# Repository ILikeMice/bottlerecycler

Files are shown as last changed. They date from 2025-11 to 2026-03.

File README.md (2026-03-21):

# PETG to Filament Bottle recycler!

https://cad.onshape.com/documents/4bfb7a9ed6c6a0026068647e/w/94f532863257475cc59f14dc/e/ca07e4d33eb1537d07c3052b

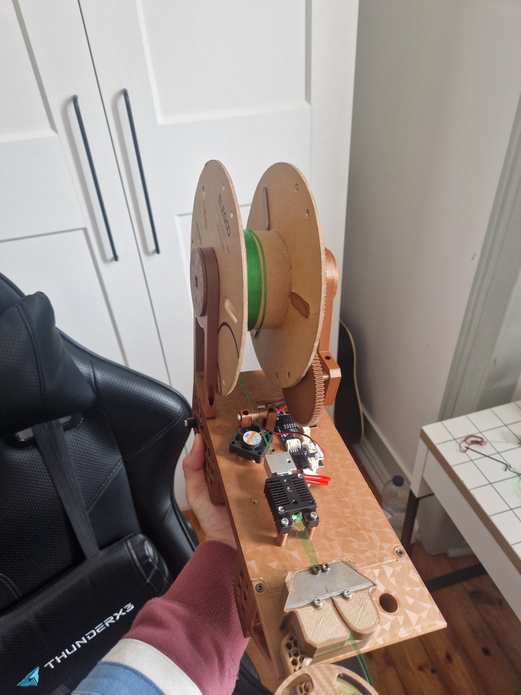
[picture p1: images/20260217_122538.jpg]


Name pretty much says it all, this is a project to try and recycle the mountain of iced tea bottles ive got into filament! Ive seen people do this years ago, but didnt really have any CAD or electronics skills back then, and really wanted to make something like that too, since 30€ per kg of filament seems overpriced and i would really prefer to spend my money on aliexpress instead.

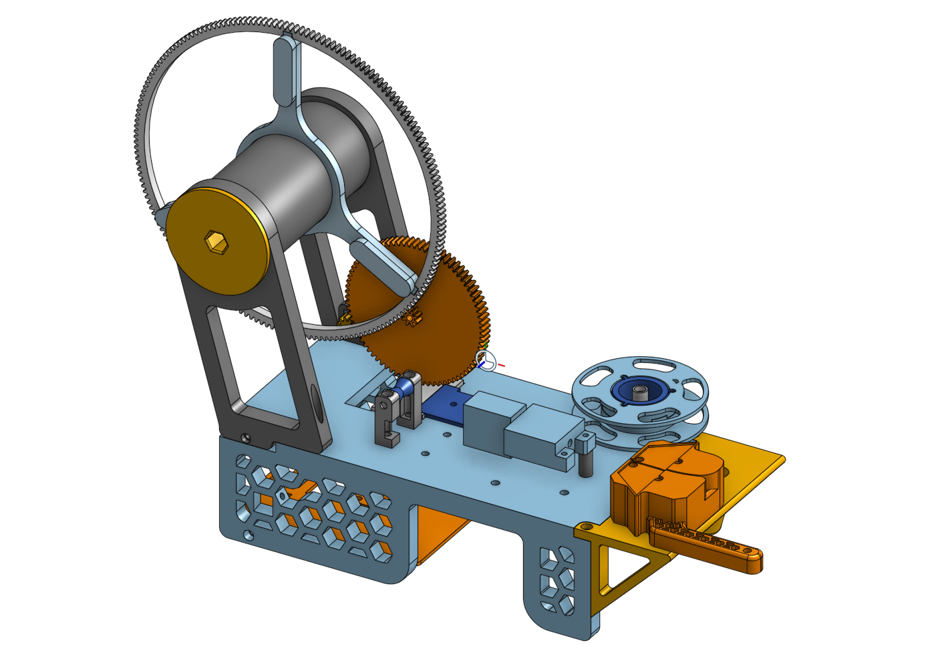
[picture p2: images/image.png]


The way it works is: plastic bottles get cut up into strips (~8mm) and pulled through the hotend, at a temp that is about enough to soften the plastic **without melting it**, so the strip gets rolled up into itself and forms some sort of a tube. I can then use this makeshift filament to print stuff!

I tried to use as many components from an Anycubic Kobra 2 Hotend in this project, since i had one laying around (and which i bought for only 10 bucks, damn good deal), and ended up using pretty much everything i could: The stepper motor from the extruder, the hotend itself(duh), practically all the screws, and even the PCB that controlled (or rather had all the connectors, the only thing except traces on that thing is a couple of diodes lol) the whole thing!

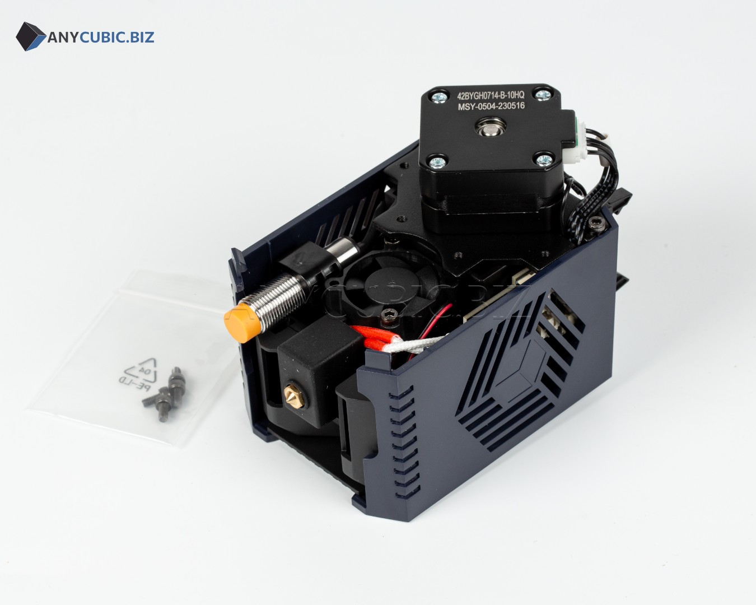
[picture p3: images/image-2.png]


The contraption itself is controlled by an ESP32, which drives a BJT for the DC motor of the spool and a Heater Element via a mosfet, with the circuit shown below!!

### Main Circuit
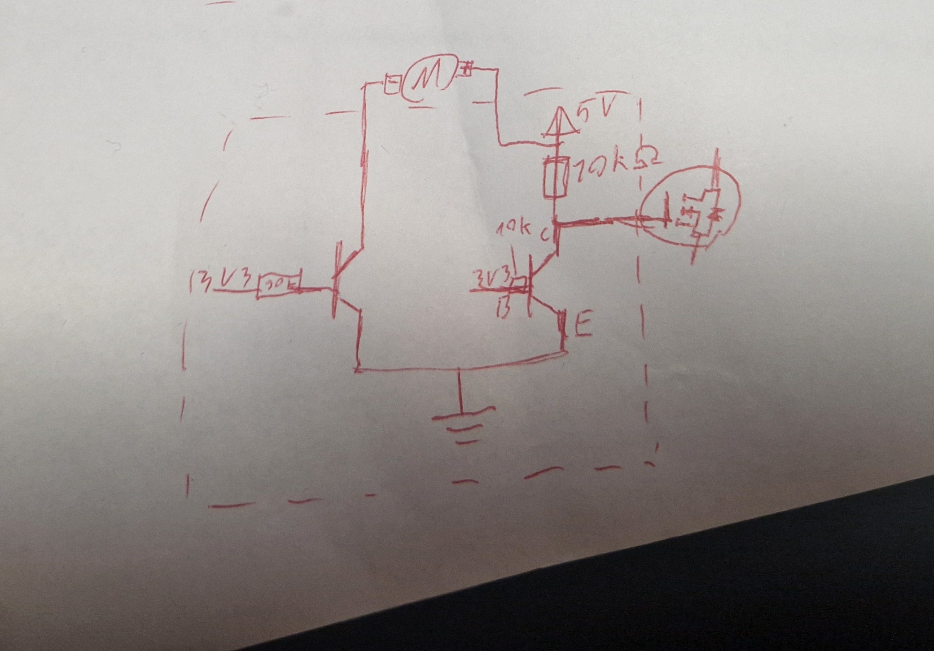
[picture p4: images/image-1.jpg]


This is the diagram of the main circuit im using, which i had to put together and solder on my own! You will also have to remove the ressistors on the IRF520 module. The circuit is used to drive the DC motor with 5v from the buck converter, and drive the MOSFET with the same 5v, since the ESP can only output up to 3.3v, and the IRF520 needs 4v  at gate.

## BOM

This is all the extra stuff i had to buy and didnt have around!

|Name |Cost (per unit. in €)|Amount|Cost (€)|Link |
|---|---|---|---|---|
|6A 24V PSU (laptop charger or sth)|15 |1 |15 |bought from local ebay |
|24V to 5A DC-DC converter |2.88 |1 |2.88 |https://www.aliexpress.com/item/1005007259901753.html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 |
|MOSFET Breakout |1.22 |1 |1.22 |https://www.aliexpress.com/item/1005008554454996.html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 |
|Trapezoidal Blade |0.89 |1 |0.89 |https://www.aliexpress.com/item/1005007677799664.html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 |
|Wire Crimps Set |3.69 |1 |3.69 |https://a.aliexpress.com/_EzglbQU |
|Stepped drill bit |1.09 |1 |1.09 |https://a.aliexpress.com/_EJElGGy |
|M3 nuts |0.39 |1 |0.39 |https://a.aliexpress.com/_EuZlNXO |
|Kobra 2 hotend. bought from ebay  |10 |1 |10 | |
|L298N |2.67 |1 |2.67 |https://pt.aliexpress.com/item/1005009503497796.html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 |
|ESP32 |3 |1 |3 |https://pt.aliexpress.com/item/1005008889768599.html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|
| | | | | |
| |Total (€): |39.81 | | |

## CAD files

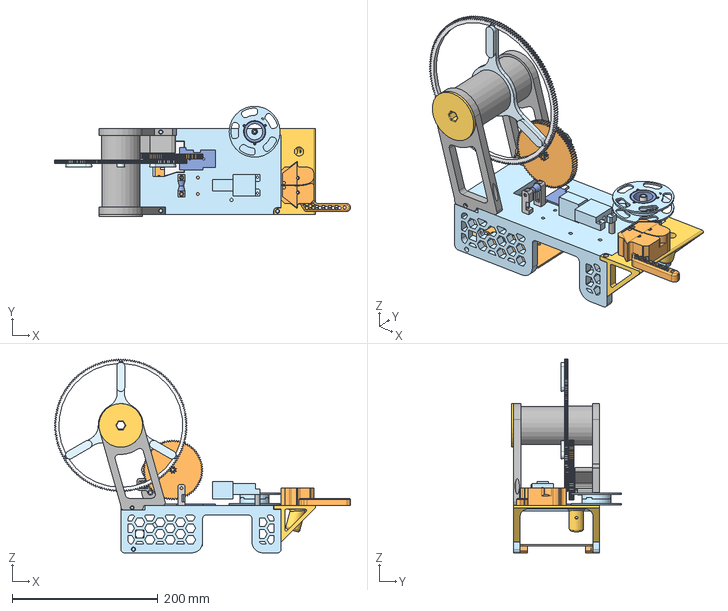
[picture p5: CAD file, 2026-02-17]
CAD/BottleToPETG(1).step
406.3 x 151.2 x 266.0 mm

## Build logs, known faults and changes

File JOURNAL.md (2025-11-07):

<!--
  ===================    !!READ THIS NOTICE!!   ====================
  DO NOT edit this file manually. Your changes WILL BE OVERWRITTEN!
  This journal is auto generated and updated by Hack Club Blueprint.
  To edit this file, please edit your journal entries on Blueprint.
  ==================================================================
-->

## 11/1/2025 3 PM - Initial research!  

Ive got an overall idea on how a pet bottle recycler works, but never really looked into the details much. I think before starting the modelling, etc. itd be better to get some info for potential future struggles and so on.
All i know so far about the process is: bottle gets sliced into strips, pulled thru an extruder and then wound onto a spool. 
After watching a bunch of vids on ppl assembling pet recyclers (didnt really get as many about the design process itself, but thats my task after all, also [this one](https://www.youtube.com/watch?v=1yIe1Pp_Nrg) was the coolest one i found, will probably be using it as a reference mainly, even though it might not be fully printed like i want it), i got an approximate plan? I can slice the bottle with some sanded bearings (which i think is really cool, i only thought of using a blade b4), as for the heating part, im currently trying to deconstruct the kobra hotend. Also, i think ill try to make this thing as compact as possible, since i dont have much space in my room :pf:

Probably the inspo ill be using throughout the project: 


## 11/1/2025 9 PM - Hotend!  




Managed to fully take apart the hotend, surprisingly without breaking anything (and did some browsing on aliexpress for the parts i dont yet have) ! Its got a pcb with some ressistors, but those seem to be for the levelling sensor, so im unsure whether ill use it or just detach all the things from it. 
After some more digging, i found out that the hotend runs at 24V, so ill need a 24V psu, but im willing to pay for all that stuff. The benefit of using the pcb though would be having every connection neatly mounted already, so on second thoughr ill try and stick with that, not like its got any other use. 
Also, while taking the thing apart, i noticed that the steppers casing is grounded for some reason (weird to me, but ill probs keep that just to be safe :p ) also would probably need to make some drilling changes for the hotend, either drill a slightly bigger intake hole with a stepless bit, or if i dont feel like drilling i might try making that transition with a 3d printed part (my own idea wow), and ill defo need to make a 1.7mm hole in the nozzle ive got already. 

Speaking again of the pcb, its got a weird mount for all the cables, but a simple jumper cable seems to fit it, but ill have to design some frame to hold them all so i can clamp them with the things at the mount. Would be cool to use though.  

## 11/2/2025 12 AM - more research yippie  

I know i need a 24V PSU, but i have no idea so far how strong it should be. since i want this to be as compact as possible, im hoping for 3A at best, 5A max. Above that the psu gets a bit big (3A is 110\*78\*36, 5A is 160\*98\*42mm, 6A is 199\*98\*42mm). After a quite some research i found that the hotend altogether is supposed to be about 24/60W, which is about 2.5A already. Also checked on the heating element itself (which gave me 60w) to confirm the power and the fact its the hotend only, not the whole toolhead with stepper and so on. I couldnt find anything googling the numbers on the stepper to get its approximate power, so i had to turn to deepseek my beloved. It suggested a max current of .66A per phase, so 1.32A max in total, so ill stick to that for now (writing on the nema17 was **_42shdb0066z-10WD_**). After detaching the small fan attached to the heatsink, i could read off 0.08A/24V from it. I could also use the bigger fan there, but itll need .2A of current, so i gotta see if ive got enough left at the end. So for now, the total current is at about **3.9A** (with the smaller fan, with the bigger one its **4.02A**). Id like some wiggle room for the controlling stuff (which i gotta power with a stepdown converter), so i think 5A should hopefully be enough. I dont need anything fancy to control the stepper, ill use a L298N driver that ive got laying around. Speaking of logic and control though, ill need something to actually control all the stuff. I could go with an orph pico ive got but that would mean id need a display, and i sadly dont have one right now (altho it would be cool to use one bc yk, this is a hc ysws). An alternative would be an ESP32/rpi zero 2 W that i gotta control via ssh or so, which would save me like 3 bucks in buttons and display. tempting. Although a display would look cooler.




## 11/2/2025 3 PM - CAD start  

After trying around a bit in freecad and taking 8 fucking minutes to make a single rectangle, i decided that i dont like freecad anymore and am switching to onshape. I did some irl mockups of how the hotend and so on could be placed, and the two options i had was either with the fan facing downwards, but pcb being below the hotend, or fan upwards and pcb being higher than the hotend, since i cant really move it much due to the cables. I tried reattaching the fan on the other side of the heatsink so it could be on top with the pcb on the bottom, but had to kinda force the screw into it from the other side to make the thread useable, no idea why they made it like that. 
Anyways, after doing that, the layout of the components seems perfectly useable, i need the hotend to be higher than the pcb because i gotta get it as far away from the plasic parts as possible, while preferrably having the pcb inside the casing. I made an approximate model of the whole hotend part in onshape, with the main details ill need for mounting, etc. Took a bit longer than estimated, since i had to get used to onshape, but overall onshape seems pretty nice. 







## 11/2/2025 9 PM - More CAD!  



Thought of how id design the casing.[ In the video i mentioned in the first devlog](https://www.youtube.com/watch?v=1yIe1Pp_Nrg), the guy was using extrusions and kinda just mounting everything on that. As cool as i thought having extrusions would be, i wanna make this as 3d printable and cheap as possible. My current idea is to have little platforms or pins to hold the psu and so on, that ill screw into the sides of the rectangular ish casing (without a bottom, to reduce material), still thinking on that though. 

Either way, main thing this session was cadding the pcb so i can make a mount for it or so. That took me waaaayyy too long since there wasnt ANY info on it online, so i had to measure anything manually (and of course i fucked up a couple times, and had constraint errors everywhere T-T, also i realized ive never really modelled after a real life complex-ish object without a schematic). After fixing everything though, it looks pretty nice and im happy with it. I wanna also make mounts ish for every pcb ill have, since this thing might be moved around a bunch and i wouldnt want the stuff to slip.  

## 11/3/2025 - Casing stuff!  





^^As you can see above, i did a bunch of improvements on the casing! Taking inspo from the design of that other guy i mentioned in the first entry, i wanted some sort of hex pattern on the casing, which looks cool but is also mainly to save some filament and printing time. Ive never really printed anything vertically with a hex pattern, and was unsure if it would hold at all. Some research told me i gotta have the flat side of the hexagon pointing up, and just bridge over it so it doesnt break. I have no idea how my printer performs in bridging, but from what ive seen online the quality is pretty meh, but using supports might just increase print  time and filament use more than this pattern is reducing. The upper version is me trying to round the corners to minimize bridging, but that way just leads to circles at the end, and im unsure of what the layer height req will be with rounded corners (does also look pretty cool tho!). Gotta run some tests ig.



Also, i got started on the electronics layout stuff and so on! Added some cool looking holders! The orange ones will be secured in place with the 2 heatset inserts and some screws ive got in the hotend/some other way, but ill be sure to definetly use those inserts, thought its really neat to use as much from the toolhead as possible. The blue ones are printed together with the case (i thought of making them flipped, so i wouldnt need support but that seemed like a pretty bad idea holding power wise) and are gonna need supports, so i placed them on the edges to be able to not have supports placed on the model itself.

PS: this shit took me way too long, im not adding all the variations i tried here and holy some of the tools (esp pattern) are so much weirder than in fusion, this shit is making me actually learn how to use constrains in sketches lmao

## 11/4/2025 - Electronics layout stuff (yay..)  



I did some of the work here yesterday, but was too tired to document it :p

First of all, made holes for screws/heatset inserts to mount the pcb and hotend (also made a hole for the pcb wire holder thing so i can connect stuff from the electronics inside the case into it)! Had to correct some little errors in the pcb model since im that good at cad. Also, minor change, changed the shape of the electonics holder mount, since printing circles would be pretty annoying and probs unstable.



Really love how i can modify the timeline to change some stuff, didnt really do that much in fusion, does take some extra time sometimes tho, but feels waaay cleaner




So, electronics layout! Dont wanna flood the whole page with the shit i tried before giving up and looking for an algorithm to find the optimal layout for me (almost pulled up python smh), the first img is one of the first things i tried making and was confident enough in to screenshot! I was then hit by the psu that i hid which was taking up too much of the space. My fault for hoping i could fit all the stuff on 1 platform ig. I was still hanging onto the idea of fitting it all on the platform for a while, all i needed was like 3mm of extra space. I then proceeded to resize the whole case (which was really painful since i also had to change the pattern thing) only to realize that its 223mm long now. Which just so happens to be about 3mm bigger than my printbed. Yeouch. The whole thing is like 110mm wide so i dont think placing it diagonally would fit it onto the printbed either. Started thinking of where i could possibly place 1 more component, first idea was to make the platform have 2 floors, but that seemed rly hard to print and overall i am not dealing with the wires on 2 whole floors. Other option would be to mount it somewhere on the case (if so, then probably on the "ceiling" of the case, since anywhere else would be too far from the components (e.g. i need the 24 to 5v converter to be not far from the esp in order to power it, and other components like the mosfet or L298N near the PSU cuz i need 24v there). After more pondering and messing around for a fuckton of time, i went with the L298N on the ceiling, and the rest on the Platform (dont have mounting holes for the components figured out yet, will after most of them arrive)  

## 11/6/2025 - Filament spool mount!  

Yippie 2 in 1 journal entry again! 
Final design today below:



Yesterday, i made the side things that are supposed to hold the spool up, see how theres like half the thing popping out at the bottom? I probably couldve just not done that but i wanted to make sure this shit does NOT wiggle, and even tho inserting a bolt from that side makes the main case look weird in places, i think its probs def better with that side mount (i still gotta add a screw to hold it down like one normally would). 

Initially, the plan for the spool was for it to be halfway "inside" the case, kinda submerged for compactness. Only reason i cant do that though is thanks to the electronics layout problem (not reexplaining that, go read previous entries) taking up way too much space, and removing any more of the case would just screw up the stability of it.



^^weird case thing because of the sideways screw, hopefully it wont break (surely not foreshadowing, _**right**_?)^^

Then today, i also did some more research on how people overall made this part. Once again taking inspo from the main inspiration design, i saw hes got a 3d printed spool and a huuuge gear around it connected to a smaller stepper gear. As much as i want to make this fully 3d printable, i did have a spool with just a bit of filament left int it. After removing that, i saved myself like 6-7 hours of print time! The spool has round holes in it, 6 in total, paired together in 3 pairs. My initial idea was to make things that clamp into those, holding a gear that i can later rotate somehow. I ended up thinking about that in the very last step, will return to this in like 1 paragraph.

I was now also stuck with a decision: either i connect the spool with a timing belt (my initial idea) or i make a huge gear thats exactly the same module as the one mounted on the stepper (cant take off the gear sadly, its part of the stepper rod :p). The timing belt did fit onto the stepper gear decently though, and that extra closed loop belt i bought was reeeealllly looking at me. biggest gear i could do with that belt was about 80T though, and the stepper ended up being way too far from the pcb :/ I didnt really want to do a big gear, since first of all, id have to print a decently big chunk of it with the smallest nozzle ive got (0.2mm), and prototyping didnt sound much fun with that either. After trying around some more though, i realized i didnt really have a choice, so i just went with that, and make a whopping 400T gear (it had to be big enough to read anywhere near the PCB) that made onshape lag yayyy! Also, decided to mount the stepper directly to one of the spool holders, since i dont think i really need a stepper frame here. I did have to manually measure everything on the stepper tho since i dont trust online sources on some random stepper that i dont have a 20823 page manual for. In total, i am left with a 40:1 reduction ratio on that thing, surely thats fine.

Back to attaching the gear to the spool! I tried using those 6 holes, but they were so conveniently placed for my inconvenience, that the teeth were right in the middle of them. Instead of trying to get it to work i just switched to the 3 rectangular ish holes on the spool. My idea of having the mounts outside the gear didnt really work with that one, i think its even better this way though, lucky the 1st version didnt work! 

The blue thing is the thing that attaches to the filament spool. Ill print it with a bigger nozzle to save time and just glue it onto the gear thing.

Biggest problem so far though was the layout of the stuff on that cylinder thats holding everything. i wanted to make everything not slip, and make sure the rod itself is somewhat detachable too, since ill need to remove the spool for, you know, printing sometime. Long story short, in the end i ended up with a design looking like a spyglass, where the things have a decreasing diameter, so theyre practically locked in place/sqished into the one holder!



Also, the spool isnt perfectly centered now, so i had to move the hotend a bit.



## 11/7/2025 - Cutting mechanism test!  

I think the winding system is pretty much done, just gotta add in some screws and maybe polish it a bit. Anyways, i wanted to test whether bearings could even cut the bottle, so i took some sandpaper and started sanding one!

I realized quite quickly that theres a reason everyone in the videos had either a belt sander or some disk thing, since sanding this thing manually was real hard, and took me like one hour in total.

Screenshot_20251107_144942_YouTube


^^ bearing in the video vs my bearing after goinf through a whole sheet of sandpaper and exhausting my hand

Ended up almost losing the bearing towards the end under the boards of the balcony (went there to not disturb anyone, this process is pretty damn loud), luckily managed to retrieve it though

In conclusion: im gonna assume it works, since compared to the unsharpened side of the bearing, the sharpened one actually leaves some scratches on the bottle, so surely itll work if i sand it just a bit more, right?

Also, im gonna try making some holder i can attach to my drill to sand this thing, no way im doing all that manually again.

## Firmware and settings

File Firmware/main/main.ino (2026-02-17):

#include <ESP8266WiFi.h>
#include <ESP8266WebServer.h>
#include <math.h>

#define THERMISTOR_PIN A0
#define MOTOR_PWM_PIN 4      // D2 pin
#define HEATER_PIN 14        // D5 pni

const char* ssid = "ssid!";
const char* password = "your pwd";

ESP8266WebServer server(80);

// this changes probably if youre using a diff thermistor!!!!
#define SERIES_RESISTOR 100000.0
#define NOMINAL_RESISTANCE 100000.0
#define NOMINAL_TEMP 25.0
#define BETA_COEFFICIENT 3950.0

#define HEATER_WINDOW_MS 1000  
#define MAX_HEATER_DUTY 200   

float Kp = 2.0;
float Ki = 1.5;
float Kd = 0.1;

// this prolly also varies depending on your hardware, but i dont think theres any case in which youll need 260C for this.
#define MAX_TEMP 260.0
#define PID_MIN_OUTPUT 0
#define PID_MAX_OUTPUT 255

float currentTempC = 0.0;
float targetTempC = 200.0;
bool autoMode = true;       
bool heaterEnabled = false;  
bool emergencyStop = false;
bool motorRunning = false;

float pidInput, pidOutput, pidSetpoint;
float lastError = 0;
float integral = 0;
unsigned long lastPidTime = 0;

float heaterDutyCycle = 0;  
unsigned long heaterWindowStart = 0;

float tempAtHeatStart = 0;
unsigned long heatStartTime = 0;
bool isHeating = false;

unsigned long lastDebug = 0;

void readTemperature() {
  const int SAMPLES = 20;
  long sum = 0;
  
  for (int i = 0; i < SAMPLES; i++) {
    sum += analogRead(THERMISTOR_PIN);
    delay(2);
  }
  
  float currentADC = sum / SAMPLES;
  
  float reading = (1023.0 / currentADC) - 1.0;
  reading = SERIES_RESISTOR / reading;
  float thermistorResistance = reading;
  float steinhart = thermistorResistance / NOMINAL_RESISTANCE;
  steinhart = log(steinhart);
  steinhart /= BETA_COEFFICIENT;
  steinhart += 1.0 / (NOMINAL_TEMP + 273.15);
  steinhart = 1.0 / steinhart;
  currentTempC = steinhart - 273.15;
  
  if (millis() - lastDebug >= 2000) {
    Serial.print("ADC:");
    Serial.print((int)currentADC);
    Serial.print(" R:");
    Serial.print((int)thermistorResistance);
    Serial.print(" temp:");
    Serial.print(currentTempC, 1);
    Serial.print("target:");
    Serial.print(targetTempC, 0);
    Serial.print("heater duty:");
    Serial.print((int)heaterDutyCycle);
    Serial.print("/255");
    if (autoMode) Serial.print(" AUTO");
    else Serial.print(" MANUAL");
    if (emergencyStop) Serial.print(" EMERGENCY");
    Serial.println();
    lastDebug = millis();
  }
}

void updatePID() {
  unsigned long now = millis();
  if (now - lastPidTime < 200) return;
  lastPidTime = now;
  
  if (!autoMode || emergencyStop || !heaterEnabled) {
    if (!heaterEnabled && autoMode) {
      heaterDutyCycle = 0;
    }
    return;
  }
  
  pidInput = currentTempC;
  pidSetpoint = targetTempC;
  
  float error = pidSetpoint - pidInput;
  
  if (abs(error) < 50) {
    integral += error * 0.2;  
  }
  integral = constrain(integral, 0, 100);
  
  float derivative = (error - lastError) / 0.2; 
  lastError = error;
  float output = (Kp * error) + (Ki * integral) + (Kd * derivative);
  output = constrain(output, PID_MIN_OUTPUT, MAX_HEATER_DUTY);
  heaterDutyCycle = output;
  
  if (heaterDutyCycle > 50) {
    if (!isHeating) {
      isHeating = true;
      tempAtHeatStart = currentTempC;
      heatStartTime = millis();
    }
  } else {
    isHeating = false;
  }
}

void updateHeater() {
  unsigned long now = millis();
  
  if (now - heaterWindowStart > HEATER_WINDOW_MS) {
    heaterWindowStart = now;
  }
  
  int onTime = (heaterDutyCycle / 255.0) * HEATER_WINDOW_MS;
  
  if (!emergencyStop && (heaterEnabled || (autoMode && heaterDutyCycle > 0))) {
    if (now - heaterWindowStart < onTime) {
      digitalWrite(HEATER_PIN, LOW);
    } else {
      digitalWrite(HEATER_PIN, HIGH); 
    }
  } else {
    digitalWrite(HEATER_PIN, HIGH);    
  }
}

void checkSafety() {
  if (currentTempC > MAX_TEMP) {
    emergencyStop = true;
    heaterEnabled = false;
    heaterDutyCycle = 0;
    digitalWrite(HEATER_PIN, HIGH);
  }
  
  if (isnan(currentTempC) || currentTempC < -10 || currentTempC > 350) {
    emergencyStop = true;
    heaterEnabled = false;
    heaterDutyCycle = 0;
    digitalWrite(HEATER_PIN, HIGH);
  }
  
}

void setMotor(bool state) {
  motorRunning = state;
  digitalWrite(MOTOR_PWM_PIN, state ? HIGH : LOW);
}

void setHeaterManual(bool state) {
  if (emergencyStop) return;
  autoMode = false;
  heaterEnabled = state;
  heaterDutyCycle = state ? MAX_HEATER_DUTY : 0;
}

void setHeaterAuto(bool enable) {
  if (emergencyStop) return;
  autoMode = true;
  heaterEnabled = enable;
  if (!enable) {
    heaterDutyCycle = 0;
    integral = 0;
    lastError = 0;
  }
}

void setTargetTemp(float temp) {
  targetTempC = constrain(temp, 0, 250);
  integral = 0;  
  lastError = 0;
}

void handleRoot() {
  String html = R"rawliteral(
<!DOCTYPE html>
<html>
<head>
  <meta name="viewport" content="width=device-width, initial-scale=1">
  <title>Extruder Control</title>
  <style>
    body { font-family: Arial; background: #1a1a1a; color: #fff; text-align: center; padding: 20px; }
    .emergency { background: #d32f2f; padding: 20px; font-size: 24px; cursor: pointer; 
                 margin-bottom: 20px; border-radius: 8px; font-weight: bold; }
    .grid { display: grid; grid-template-columns: 1fr 1fr; gap: 20px; max-width: 700px; margin: 0 auto; }
    .card { background: #333; padding: 20px; border-radius: 12px; }
    .temp { font-size: 48px; color: #ff9800; }
    .target { font-size: 36px; color: #4CAF50; }
    .status { font-size: 20px; margin: 10px 0; }
    .on { color: #4CAF50; }
    .off { color: #666; }
    .heating { color: #ff9800; }
    button { padding: 15px 30px; font-size: 16px; margin: 5px; border: none; 
             border-radius: 8px; cursor: pointer; }
    .heat-auto { background: #ff9800; color: #000; }
    .heat-man { background: #9c27b0; color: #fff; }
    .heat-off { background: #555; color: #fff; }
    .motor-on { background: #2196F3; color: #fff; }
    .motor-off { background: #555; color: #fff; }
    .pid-box { background: #222; padding: 10px; border-radius: 8px; margin-top: 10px; font-size: 14px; }
    input[type=number] { width: 60px; font-size: 16px; }
    .warning { color: #ff6b6b; font-weight: bold; margin-top: 10px; }
    .mode-auto { border: 2px solid #ff9800; }
    .mode-man { border: 2px solid #9c27b0; }
  </style>
</head>
<body>
  <h1>Extruder Control</h1>
  
  <div class="emergency" onclick="fetch('/stop').then(update)">EMERGENCY STOP</div>
  
  <div class="grid">
    <div class="card">
      <div>Current Temperature</div>
      <div class="temp" id="temp">--°C</div>
      <div class="status" id="pidStatus">PID: --</div>
    </div>
    
    <div class="card">
      <div>Target Temperature</div>
      <div class="target" id="target">--°C</div>
      <input type="number" id="targetInput" value="200" min="0" max="250" 
             onchange="setTarget(this.value)" style="margin-top: 10px;">
      <button onclick="setTarget(document.getElementById('targetInput').value)" 
              style="padding: 10px 20px;">Set Target</button>
    </div>
    
    <div class="card" id="heaterCard">
      <div>Heater Control</div>
      <div class="status" id="heaterStatus">Mode: --</div>
      <div class="status" id="dutyStatus">Duty: --%</div>
      <button onclick="setHeater('auto')" class="heat-auto">Auto PID</button>
      <button onclick="setHeater('manual')" class="heat-man">Manual ON</button>
      <button onclick="setHeater('off')" class="heat-off">OFF</button>
      <div class="pid-box">
        Kp: <input type="number" id="kp" value="12" step="0.5" onchange="tunePID()">
        Ki: <input type="number" id="ki" value="0.4" step="0.1" onchange="tunePID()">
        Kd: <input type="number" id="kd" value="80" step="5" onchange="tunePID()">
      </div>
    </div>
    
    <div class="card">
      <div>Motor Control</div>
      <div class="status" id="motorStatus">Motor: --</div>
      <button id="motorBtn" onclick="toggleMotor()" class="motor-off">Toggle Motor</button>
      <div class="warning" id="emergency" style="display:none">EMERGENCY STOP ACTIVE</div>
    </div>
  </div>

  <script>
    function update() {
      fetch('/status')
        .then(r => r.json())
        .then(d => {
          document.getElementById('temp').innerText = d.temp.toFixed(1) + '°C';
          document.getElementById('target').innerText = d.target.toFixed(0) + '°C';
          document.getElementById('targetInput').value = d.target.toFixed(0);
          
          let hStatus = document.getElementById('heaterStatus');
          let dStatus = document.getElementById('dutyStatus');
          let hCard = document.getElementById('heaterCard');
          
          if (d.auto) {
            hStatus.innerText = 'Mode: AUTO PID';
            hStatus.className = 'status heating';
            hCard.className = 'card mode-auto';
          } else if (d.heater) {
            hStatus.innerText = 'Mode: MANUAL';
            hStatus.className = 'status on';
            hCard.className = 'card mode-man';
          } else {
            hStatus.innerText = 'Mode: OFF';
            hStatus.className = 'status off';
            hCard.className = 'card';
          }
          
          dStatus.innerText = 'Duty: ' + (d.duty / 2.55).toFixed(0) + '%';
          document.getElementById('pidStatus').innerText = 'PID out: ' + d.duty.toFixed(0) + '/255';
          
          let mStatus = document.getElementById('motorStatus');
          mStatus.innerText = 'Motor: ' + (d.motor ? 'ON' : 'OFF');
          mStatus.className = 'status ' + (d.motor ? 'on' : 'off');
          
          document.getElementById('motorBtn').className = d.motor ? 'motor-on' : 'motor-off';
          
          document.getElementById('emergency').style.display = d.emergency ? 'block' : 'none';
          if (d.emergency) document.body.style.background = '#4a0000';
          
          // Update PID inputs if different
          if (Math.abs(document.getElementById('kp').value - d.kp) > 0.1)
            document.getElementById('kp').value = d.kp;
          if (Math.abs(document.getElementById('ki').value - d.ki) > 0.01)
            document.getElementById('ki').value = d.ki;
          if (Math.abs(document.getElementById('kd').value - d.kd) > 1)
            document.getElementById('kd').value = d.kd;
        });
    }
    
    function setTarget(val) {
      fetch('/target?val=' + val);
    }
    
    function setHeater(mode) {
      fetch('/heater/' + mode).then(update);
    }
    
    function toggleMotor() {
      fetch('/motor/toggle').then(update);
    }
    
    function tunePID() {
      let kp = document.getElementById('kp').value;
      let ki = document.getElementById('ki').value;
      let kd = document.getElementById('kd').value;
      fetch('/tune?kp=' + kp + '&ki=' + ki + '&kd=' + kd);
    }
    
    setInterval(update, 500);
    update();
  </script>
</body>
</html>
)rawliteral";

  server.send(200, "text/html", html);
}

void handleStatus() {
  String json = "{\"temp\":" + String(currentTempC) + 
                ",\"target\":" + String(targetTempC) +
                ",\"duty\":" + String(heaterDutyCycle) +
                ",\"heater\":" + (heaterEnabled ? "true" : "false") +
                ",\"auto\":" + (autoMode ? "true" : "false") +
                ",\"motor\":" + (motorRunning ? "true" : "false") +
                ",\"emergency\":" + (emergencyStop ? "true" : "false") +
                ",\"kp\":" + String(Kp) +
                ",\"ki\":" + String(Ki) +
                ",\"kd\":" + String(Kd) + "}";
  server.send(200, "application/json", json);
}

void handleTarget() {
  if (server.hasArg("val")) {
    setTargetTemp(server.arg("val").toFloat());
  }
  server.send(200, "text/plain", String(targetTempC));
}

void handleHeaterAuto() {
  setHeaterAuto(true);
  server.send(200, "text/plain", "AUTO");
}

void handleHeaterManual() {
  setHeaterManual(true);
  server.send(200, "text/plain", "MANUAL");
}

void handleHeaterOff() {
  heaterEnabled = false;
  heaterDutyCycle = 0;
  integral = 0;
  server.send(200, "text/plain", "OFF");
}

void handleMotorToggle() {
  setMotor(!motorRunning);
  server.send(200, "text/plain", motorRunning ? "ON" : "OFF");
}

void handleTune() {
  if (server.hasArg("kp")) Kp = server.arg("kp").toFloat();
  if (server.hasArg("ki")) Ki = server.arg("ki").toFloat();
  if (server.hasArg("kd")) {Kd = server.arg("kd").toFloat();}
  integral = 0;
  server.send(200, "text/plain", "OK");
}

void handleStop() {
  emergencyStop = true;
  heaterEnabled = false;
  heaterDutyCycle = 0;
  motorRunning = false;
  digitalWrite(HEATER_PIN, HIGH);
  digitalWrite(MOTOR_PWM_PIN, LOW);
  server.send(200, "text/plain", "STOP");
}

void handleReset() {
  emergencyStop = false;
  integral = 0;
  lastError = 0;
  server.send(200, "text/plain", "RESET");
}

void setup() {
  Serial.begin(115200);
  delay(1000);
  
  pinMode(MOTOR_PWM_PIN, OUTPUT);
  pinMode(HEATER_PIN, OUTPUT);
  
  digitalWrite(MOTOR_PWM_PIN, LOW);
  digitalWrite(HEATER_PIN, HIGH);  // HIGH = MOSFET OFF
  
  WiFi.begin(ssid, password);
  Serial.print("Connecting to WiFi");
  while (WiFi.status() != WL_CONNECTED) {
    delay(500);
    Serial.print(".");
  }
  Serial.println();
  Serial.print("IP address: ");
  Serial.println(WiFi.localIP());
  
  server.on("/", handleRoot);
  server.on("/status", handleStatus);
  server.on("/target", handleTarget);
  server.on("/heater/auto", handleHeaterAuto);
  server.on("/heater/manual", handleHeaterManual);
  server.on("/heater/off", handleHeaterOff);
  server.on("/motor/toggle", handleMotorToggle);
  server.on("/tune", handleTune);
  server.on("/stop", handleStop);
  server.on("/reset", handleReset);
  
  server.begin();
  heaterWindowStart = millis();
  lastDebug = millis();
  Serial.println("Extruder PID Controller Started");
  Serial.println("Default target: " + String(targetTempC) + "C");
}

void loop() {
  server.handleClient();
  readTemperature();
  checkSafety();
  updatePID();
  updateHeater();
  delay(5);
}

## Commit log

2025-12-14 csv update?
    [BOM.csv]
2025-12-14 updated the BOM to list ALL the components
    [BOM.csv]
2026-02-17 step file
    [BottleToPETG(1).step, BottleToPETG.step]
2026-02-17 bom update!
2026-03-08 Update BOM.csv with new items and costs
    [BOM.csv]
2026-03-16 Update README with project details and BOM
2026-03-21 Revise BOM and project description in README
    Updated the README file to include additional components and costs for the PETG to Filament Bottle recycler project.
